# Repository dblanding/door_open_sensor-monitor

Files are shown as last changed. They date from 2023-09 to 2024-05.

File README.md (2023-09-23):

# Door Open Sensor & Monitor

## Here's the problem:

* In general, I try to keep the garage door closed except when it needs to be open.
* If I happen to be constantly going in and out (say I'm working in the yard), I leave it open.
* Occasionally, I will wake up in the morning and realize that I left the door open all night.
* Apparently, I need a reminder at the end of the day (before going to bed) to close the garage door if it is open.

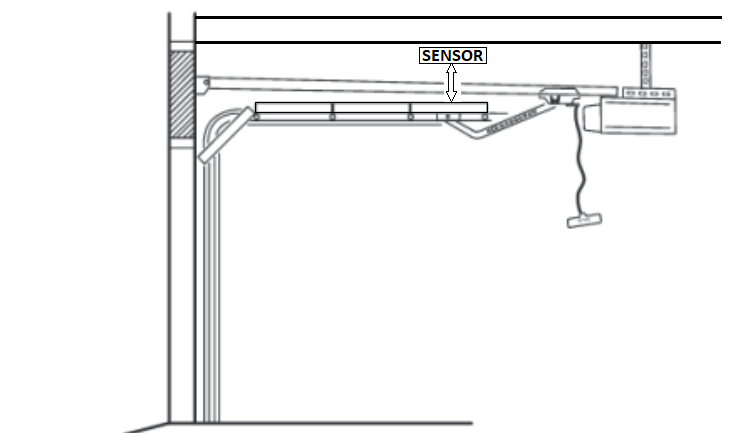
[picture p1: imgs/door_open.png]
door open schematic


## Here's the solution: Using micropython programs on Raspberry Pi Pico-W microcontrollers

* A **distance sensor** detects the presence of the garage door in the open position
    * The sensor publishes the distance on a webserver
* A remotely located **monitor** periodically requests the distance value from the sensor
    * The monitor (located where I will notice it before going to bed) flashes its onboard LED at a **rate** which is **tri-modal**:
        * 5 flashes per second if the door is open (distance is below a threshold value)
        * 1 flash per second if the door is closed (distance exceeds the threshold value)
        * 1 flash every 5 seconds if the distance value was not received

## Unanticipated problems (RF Interference with garage door opener)

### Welcome to real life!

* As anyone who has ever impemented a simple solution to a simple problem realizes, Murphy's Law is there to remind us that we have overlooked something.
* My first solution used a **VL53LOX VCSEL sensor** to measure the distance to the garage door.
    * Problem was that when the VCSEL was running, my garage door receiver was not responsive to button presses from the remote radio transmitter.
    * Apparently, the VCSEL circuitry generates RFI at a frequency that interferes with the operation of the opener's radio signal.
* My next solution was to try a **TF-Mini optical Lidar** module that I happened to have laying around.
    * Same problem
* Eventually, I used the **HC-SR04 ultrasonic distance sensor**.
    * It did the job and didn't generate RFI that interfered with the operation of the garage door opener radio signals.

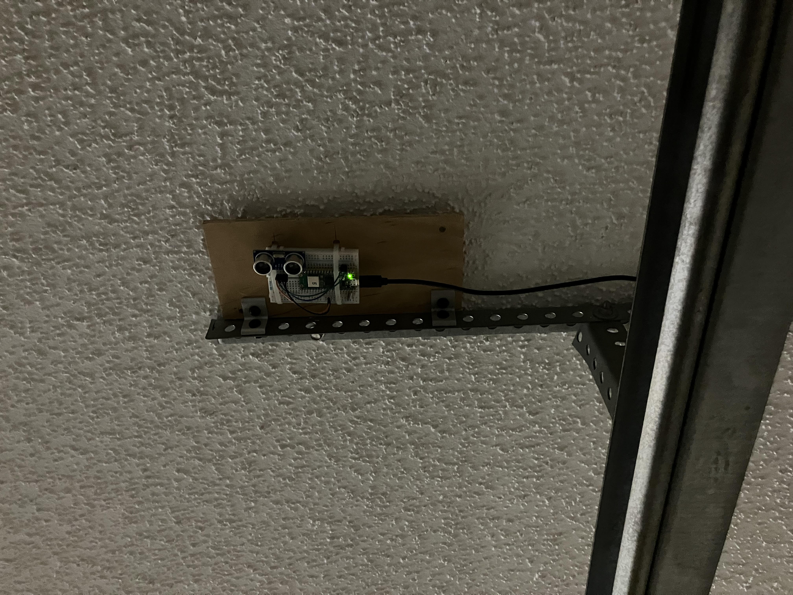
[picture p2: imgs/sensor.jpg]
Sensor board


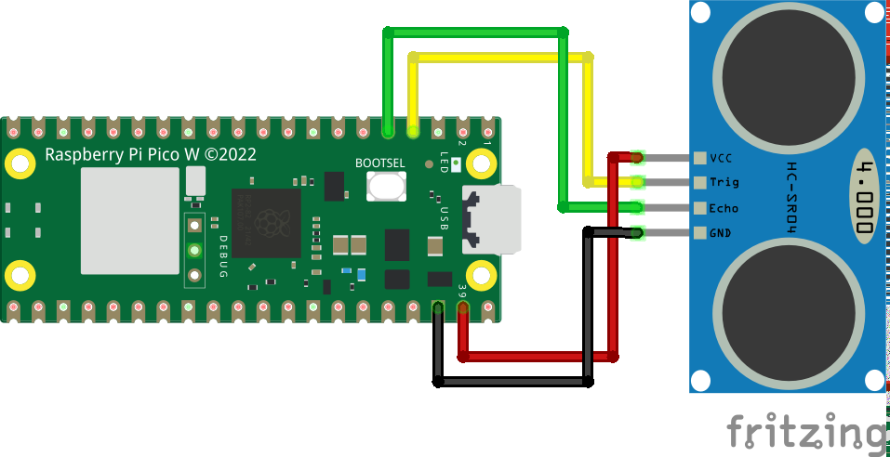
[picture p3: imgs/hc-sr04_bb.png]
Breadboard Diagram


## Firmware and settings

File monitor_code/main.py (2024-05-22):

"""
MicroPython web client for monitoring distance sensor
and displaying whether object is detected (door open).
LED flashes 5x per second when door is detected (0 < dist < 200mm).
elif dist > 200mm, LED toggles once per second.
If unable to reach server, LED toggles once per 5 seconds.
Power Failure tolerant
"""

import gc
import json
import network
import uasyncio as asyncio
from machine import Pin, I2C
import time
from secrets import secrets
import urequests as requests

ssid = secrets['ssid']
password = secrets['wifi_password']
ERROR_LOG_FILENAME = 'error_log.txt'

# setup onboard LED
led = Pin("LED", Pin.OUT, value=0)

wlan = network.WLAN(network.STA_IF)

def connect():
    """Return True on successful connection, otherwise False"""
    wlan.active(True)
    wlan.config(pm = 0xa11140) # Disable power-save mode
    wlan.connect(ssid, password)

    max_wait = 10
    while max_wait > 0:
        if wlan.status() < 0 or wlan.status() >= 3:
            print("wlan.status =", wlan.status())
            break
        max_wait -= 1
        print('waiting for connection...')
        time.sleep(1)

    if not wlan.isconnected():
        return False
    else:
        print('connected')
        status = wlan.ifconfig()
        print('ip = ' + status[0])
        return True

async def get_distance():
    """
    Get json data from server
    Return value of "distance"
    """
    headers = {'Accept': 'application/json'}
    dist  = -1
    try:
        resp = requests.get("http://192.168.1.65/", timeout=1.0)
        msg = resp.json()
        dist = msg["distance"]
    except OSError:
        pass
    return dist

async def main():
    """
    Get distance from sensor every 5 sec
    Flash LED
        Quickly if door is open
        Otherwise once per second.
    """
    print('Connecting to Network...')
    connect()
    dist = 0
    count = 0  # seconds between readings
    while True:
        # Test WiFi connection twice per minute
        if count % 30 == 0:
            count = 0
            if not wlan.isconnected():
                wlan.disconnect()
                success = connect()

        if count % 5 == 0:
            dist = await get_distance()
            # print(dist)

        if 0 < dist < 400:
            # Quick flash LED
            for rep in range(10):
                led.toggle()
                await asyncio.sleep(0.1)
        elif dist > 400:
            # Blink LED once per second
            led.on()
            await asyncio.sleep(0.1)
            led.off()
            await asyncio.sleep(0.9)
        else:
            # Blink LED once every 5 seconds
            led.on()
            await asyncio.sleep(0.1)
            led.off()
            await asyncio.sleep(4.9)
        count += 1
try:
    asyncio.run(main())
except Exception as e:
    with open(ERROR_LOG_FILENAME, 'a') as f:
        f.write(e)
finally:
    asyncio.new_event_loop()

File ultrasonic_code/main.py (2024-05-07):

"""
MicroPython webserver for distance sensor project
* Uses HCSR04 ultrasonic distance sensor
* Asynchrounous webserver reports distance (mm) in json format
Power failure tolerant
"""

import gc
import json
import network
import uasyncio as asyncio
import _thread
from machine import Pin, I2C
import time
from secrets import secrets
from hcsr04 import HCSR04

ssid = secrets['ssid']
password = secrets['wifi_password']

# setup onboard LED
led = Pin("LED", Pin.OUT, value=0)

# setup ultrasonic distanc sensor
sensor = HCSR04(trigger_pin=2, echo_pin=3, echo_timeout_us=10000)

wlan = network.WLAN(network.STA_IF)

def connect():
    """Return True on successful connection, otherwise False"""
    wlan.active(True)
    wlan.config(pm = 0xa11140) # Disable power-save mode
    wlan.connect(ssid, password)

    max_wait = 10
    while max_wait > 0:
        if wlan.status() < 0 or wlan.status() >= 3:
            print("wlan.status =", wlan.status())
            break
        max_wait -= 1
        print('waiting for connection...')
        time.sleep(1)

    if not wlan.isconnected():
        return False
    else:
        print('connected')
        status = wlan.ifconfig()
        print('ip = ' + status[0])
        return True

async def serve_client(reader, writer):
    print("Client connected")
    request_line = await reader.readline()
    request_line = str(request_line)
    # We are not interested in HTTP request headers, skip them
    while await reader.readline() != b"\r\n":
        pass

    distance = sensor.distance_mm()
    print(distance)
    mydict = {"distance": distance}
    response = json.dumps(mydict)
    writer.write('HTTP/1.1 200 OK\r\nContent-Type: application/json\r\n\r\n')
    writer.write(response)

    await writer.drain()
    await writer.wait_closed()
    # print("Client disconnected")

async def main():
    print('Connecting to Network...')
    connect()

    print('Setting up webserver...')
    asyncio.create_task(asyncio.start_server(serve_client, "0.0.0.0", 80))

    loop_count = 0
    while True:
        # Test WiFi connection twice per minute
        if loop_count == 30:
            loop_count = 0
            if not wlan.isconnected():
                wlan.disconnect()
                success = connect()

        # Flash LED
        led.on()
        await asyncio.sleep(0.1)
        led.off()
        await asyncio.sleep(0.9)

try:
    asyncio.run(main())
finally:
    asyncio.new_event_loop()

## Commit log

2023-09-15 Add Fritzing breadboard image
    [hcs04.fzz]
2023-09-15 modified WiFi connect code to retry upon failure and reconnect when dropped.
    [main.py]
2024-05-07 Modify ultrasonic & monitor code to re-connect after power failure
    [main.py]
2024-05-22 address problem of 'monitor stops flashing'
    [main.py]
